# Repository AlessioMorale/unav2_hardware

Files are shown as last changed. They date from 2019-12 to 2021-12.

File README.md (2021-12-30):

View this project on [CADLAB.io](https://cadlab.io/project/25058). 

# unav2_hardware
Initial test hardware for the future STM32F4 based uNav motor controller

## baseboard
An initial, unfinished and untested attempt to design a modular design.

## integrated_board
This is the first iteration of the testing hardware. It is being built but is not tested yet.
[more information](integrated_board/README.md)

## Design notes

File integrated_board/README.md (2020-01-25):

# Integrated Board
This is the first iteration of test hardware for unav2. The board includes a STM32F405 and two DRV8871 drivers.
It supports motor current feedback using two INA186 and global battery current/voltage monitor using an INA219.
Additionally there is an LM75 temperature monitor ic and a fan output.

Link to [Interactive BOM](https://htmlpreview.github.io/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) (built with the awesome [InteractiveHtmlBom plugin](https://github.com/openscopeproject/InteractiveHtmlBom) )

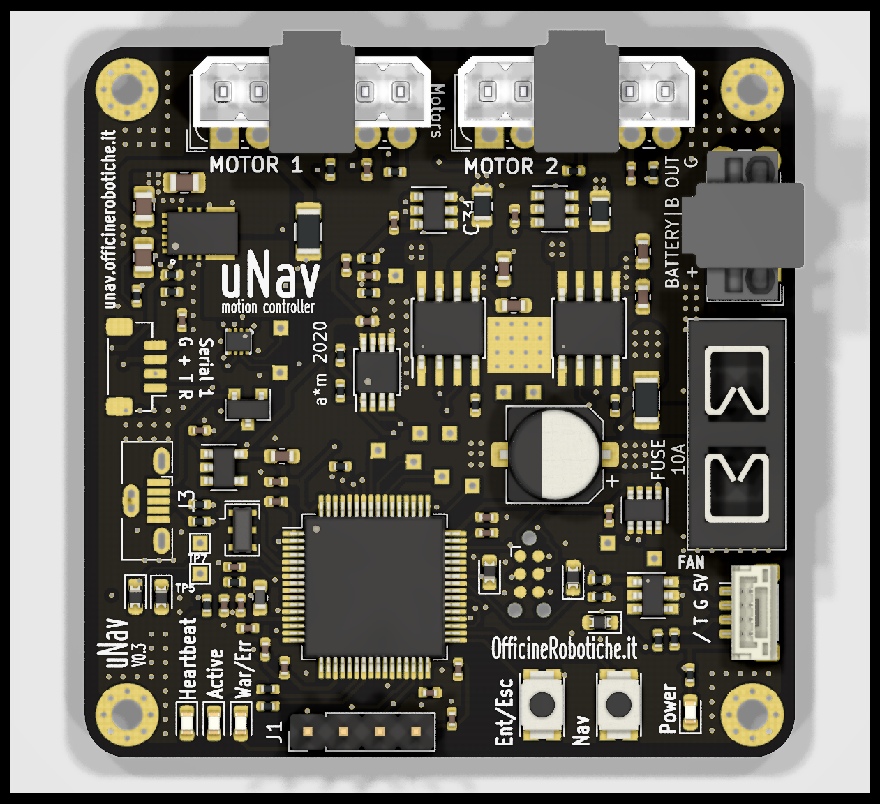
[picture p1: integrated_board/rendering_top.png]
Board top

Note: Encoder, serial and fan connectors are actually JST SH series, not exactly the type shown.

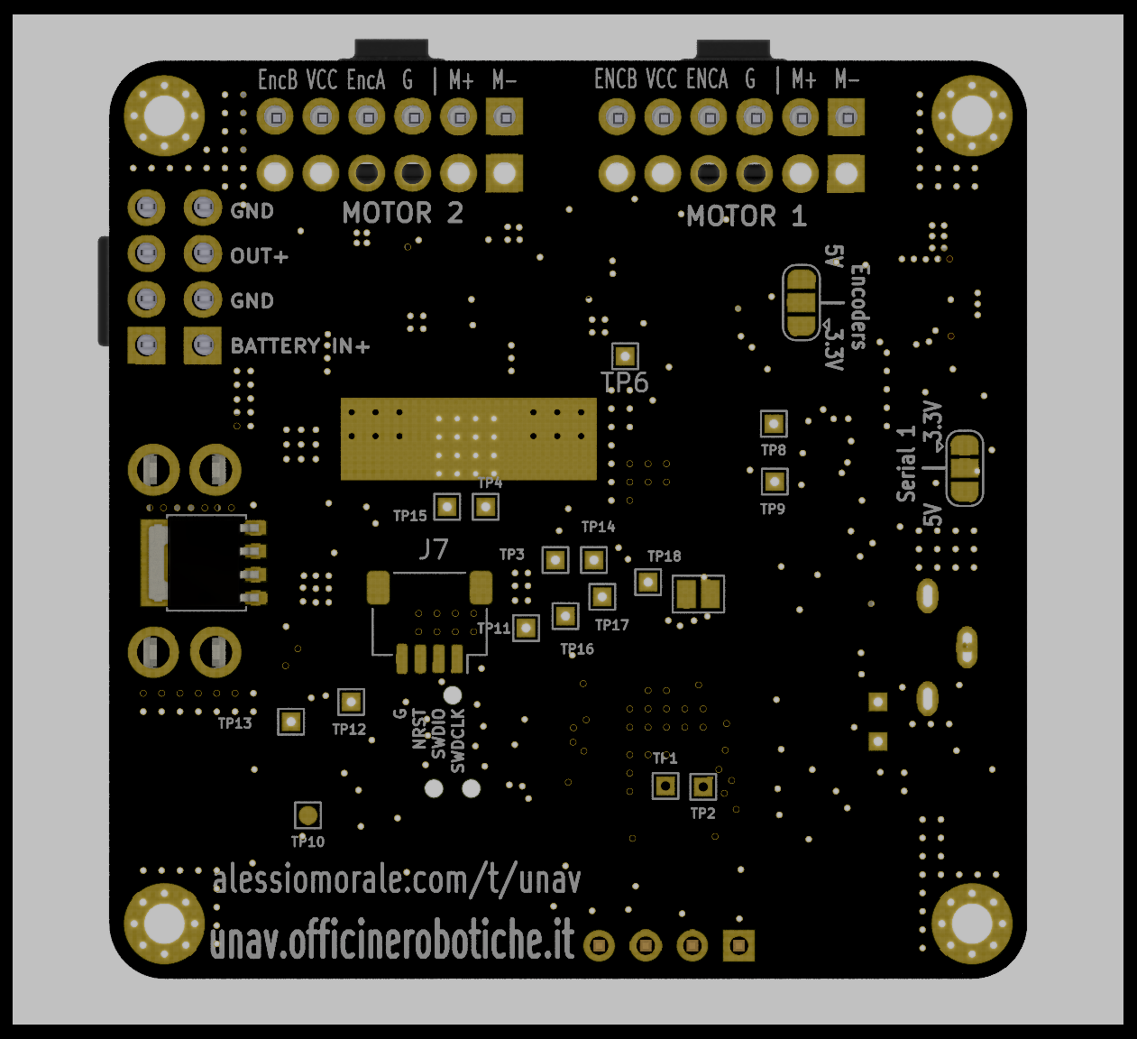
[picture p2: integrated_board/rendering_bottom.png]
Board bottom


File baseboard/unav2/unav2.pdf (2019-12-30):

## unav2 Project Configuration Report

# 1. Description

## 1.1. Project

Project Name | unav2
Board Name | custom
Generated with: | STM32CubeMX 5.2.0
Date | 08/10/2019

## 1.2. MCU

MCU Series | STM32F4
MCU Line | STM32F407/417
MCU name | STM32F407VETx
MCU Package | LQFP100
MCU Pin number | 100

# 2. Pinout Configuration

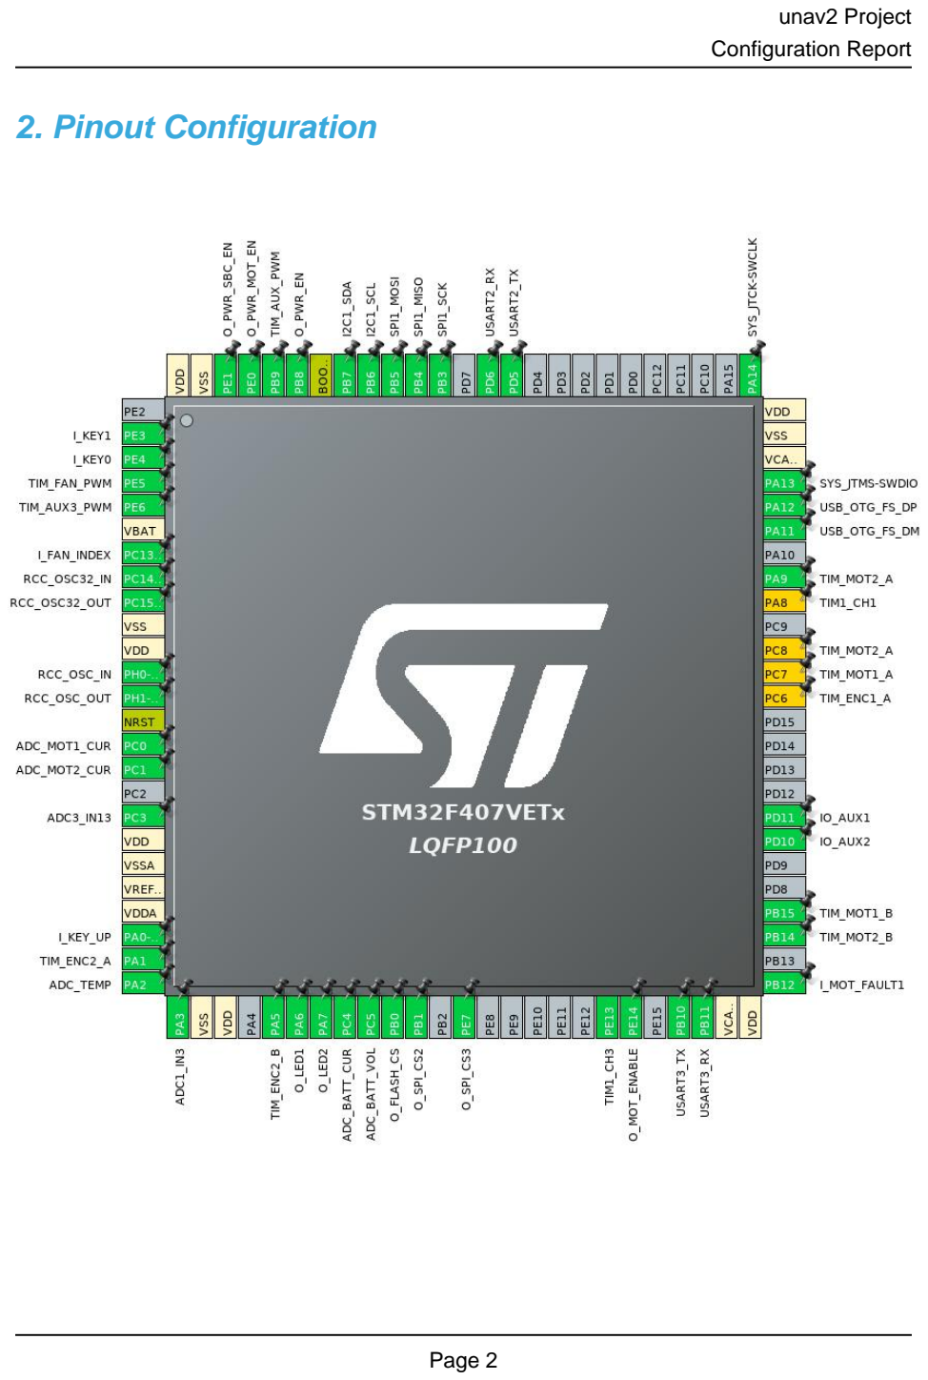
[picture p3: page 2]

# 3. Pins Configuration

Pin Number LQFP100 | Pin Name (function after reset) | Pin Type | Alternate Function(s) | Label
2 | PE3 * | I/O | GPIO_Input | I_KEY1
3 | PE4 * | I/O | GPIO_Input | I_KEY0
4 | PE5 | I/O | TIM9_CH1 | TIM_FAN_PWM
5 | PE6 | I/O | TIM9_CH2 | TIM_AUX3_PWM
6 | VBAT | Power
7 | PC13-ANTI_TAMP * | I/O | GPIO_Input | I_FAN_INDEX
8 | PC14-OSC32_IN | I/O | RCC_OSC32_IN
9 | PC15-OSC32_OUT | I/O | RCC_OSC32_OUT
10 | VSS | Power
11 | VDD | Power
12 | PH0-OSC_IN | I/O | RCC_OSC_IN
13 | PH1-OSC_OUT | I/O | RCC_OSC_OUT
14 | NRST | Reset
15 | PC0 | I/O | ADC2_IN10 | ADC_MOT1_CUR
16 | PC1 | I/O | ADC2_IN11 | ADC_MOT2_CUR
18 | PC3 | I/O | ADC3_IN13
19 | VDD | Power
20 | VSSA | Power
21 | VREF+ | Power
22 | VDDA | Power
23 | PA0-WKUP | I/O | GPIO_EXTI0 | I_KEY_UP
24 | PA1 | I/O | TIM2_CH2 | TIM_ENC2_A
25 | PA2 | I/O | ADC1_IN2 | ADC_TEMP
26 | PA3 | I/O | ADC1_IN3
27 | VSS | Power
28 | VDD | Power
30 | PA5 | I/O | TIM2_CH1 | TIM_ENC2_B
31 | PA6 | I/O | TIM13_CH1 | O_LED1
32 | PA7 | I/O | TIM14_CH1 | O_LED2
33 | PC4 | I/O | ADC1_IN14 | ADC_BATT_CUR
34 | PC5 | I/O | ADC1_IN15 | ADC_BATT_VOL
35 | PB0 * | I/O | GPIO_Output | O_FLASH_CS
36 | PB1 * | I/O | GPIO_Output | O_SPI_CS2
38 | PE7 * | I/O | GPIO_Output | O_SPI_CS3
44 | PE13 | I/O | TIM1_CH3
45 | PE14 * | I/O | GPIO_Output | O_MOT_ENABLE

Pin Number LQFP100 | Pin Name (function after reset) | Pin Type | Alternate Function(s) | Label
47 | PB10 | I/O | USART3_TX
48 | PB11 | I/O | USART3_RX
49 | VCAP_1 | Power
50 | VDD | Power
51 | PB12 | I/O | GPIO_EXTI12 | I_MOT_FAULT1
53 | PB14 | I/O | TIM1_CH2N | TIM_MOT2_B
54 | PB15 | I/O | TIM1_CH3N | TIM_MOT1_B
57 | PD10 * | I/O | GPIO_Input | IO_AUX2
58 | PD11 * | I/O | GPIO_Output | IO_AUX1
63 | PC6 ** | I/O | TIM3_CH1 | TIM_ENC1_A
64 | PC7 ** | I/O | TIM8_CH2 | TIM_MOT1_A
65 | PC8 ** | I/O | TIM8_CH3 | TIM_MOT2_A
67 | PA8 ** | I/O | TIM1_CH1
68 | PA9 | I/O | TIM1_CH2 | TIM_MOT2_A
70 | PA11 | I/O | USB_OTG_FS_DM
71 | PA12 | I/O | USB_OTG_FS_DP
72 | PA13 | I/O | SYS_JTMS-SWDIO
73 | VCAP_2 | Power
74 | VSS | Power
75 | VDD | Power
76 | PA14 | I/O | SYS_JTCK-SWCLK
86 | PD5 | I/O | USART2_TX
87 | PD6 | I/O | USART2_RX
89 | PB3 | I/O | SPI1_SCK
90 | PB4 | I/O | SPI1_MISO
91 | PB5 | I/O | SPI1_MOSI
92 | PB6 | I/O | I2C1_SCL
93 | PB7 | I/O | I2C1_SDA
94 | BOOT0 | Boot
95 | PB8 * | I/O | GPIO_Output | O_PWR_EN
96 | PB9 | I/O | TIM11_CH1 | TIM_AUX_PWM
97 | PE0 * | I/O | GPIO_Output | O_PWR_MOT_EN
98 | PE1 * | I/O | GPIO_Output | O_PWR_SBC_EN
99 | VSS | Power
100 | VDD | Power

## * The pin is affected with an I/O function ** The pin is affected with a peripheral function but no peripheral mode is activated

# 4. Clock Tree Configuration

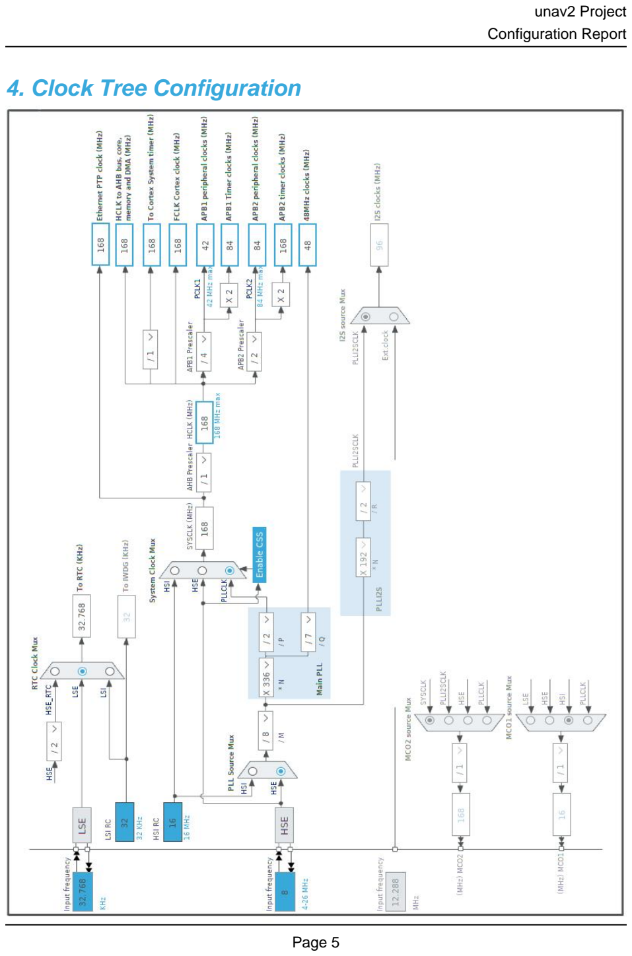
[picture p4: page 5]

# 5. Software Project

## 5.1. Project Settings

Name | Value
Project Name | unav2
Project Folder | /home/alessio/code/hardware/unav2/baseboard/unav2
Toolchain / IDE | Makefile
Firmware Package Name and Version | STM32Cube FW_F4 V1.24.1

## 5.2. Code Generation Settings

Name | Value
STM32Cube Firmware Library Package | Copy all used libraries into the project folder
Generate peripheral initialization as a pair of '.c/.h' files | Yes
Backup previously generated files when re-generating | No
Delete previously generated files when not re-generated | No
Set all free pins as analog (to optimize the power consumption) | No

# 6. Power Consumption Calculator report

### 6.1. Microcontroller Selection

Series | STM32F4
Line | STM32F407/417
MCU | STM32F407VETx
Datasheet | 022152_Rev8

### 6.2. Parameter Selection

Temperature | 25
Vdd | 3.3

# 7. IPs and Middleware Configuration

# 7.1. ADC1

## mode: IN2 mode: IN3 mode: IN14 mode: IN15 mode: Temperature Sensor Channel mode: Vrefint Channel mode: Vbat Channel 7.1.1. Parameter Settings:

### ADCs_Common_Settings:

Mode | Independent mode

### ADC_Settings:

Clock Prescaler | PCLK2 divided by 6 *
Resolution | 12 bits (15 ADC Clock cycles)
Data Alignment | Right alignment
Scan Conversion Mode | Disabled
Continuous Conversion Mode | Disabled
Discontinuous Conversion Mode | Disabled
DMA Continuous Requests | Disabled
End Of Conversion Selection | EOC flag at the end of single channel conversion

### ADC_Regular_ConversionMode:

Number Of Conversion | 1
External Trigger Conversion Source | Regular Conversion launched by software
External Trigger Conversion Edge | None
Rank | 1
Channel | Channel Vbat *
Sampling Time | 3 Cycles

### ADC_Injected_ConversionMode:

Number Of Conversions | 0

### WatchDog:

Enable Analog WatchDog Mode | false

# 7.2. ADC2

## mode: IN10 mode: IN11 7.2.1. Parameter Settings:

### ADCs_Common_Settings:

Mode | Independent mode

### ADC_Settings:

Clock Prescaler | PCLK2 divided by 6 *
Resolution | 12 bits (15 ADC Clock cycles)
Data Alignment | Right alignment
Scan Conversion Mode | Enabled
Continuous Conversion Mode | Disabled
Discontinuous Conversion Mode | Enabled *
Number Of Discontinuous Conversions | 1
DMA Continuous Requests | Enabled *
End Of Conversion Selection | EOC flag at the end of all conversions *

### ADC_Regular_ConversionMode:

Number Of Conversion | 4 *
External Trigger Conversion Source | Timer 8 Trigger Out event *
External Trigger Conversion Edge | Trigger detection on the rising edge
Rank | 1
Channel | Channel 10
Sampling Time | 28 Cycles *
Rank | 2 *
Channel | Channel 11 *
Sampling Time | 28 Cycles *
Rank | 3 *
Channel | Channel 10
Sampling Time | 28 Cycles *
Rank | 4 *
Channel | Channel 11 *
Sampling Time | 28 Cycles *

### ADC_Injected_ConversionMode:

Number Of Conversions | 0

### WatchDog:

Enable Analog WatchDog Mode | false

# 7.3. ADC3

## mode: IN13 7.3.1. Parameter Settings:

### ADCs_Common_Settings:

Mode | Independent mode

### ADC_Settings:

Clock Prescaler | PCLK2 divided by 6 *
Resolution | 12 bits (15 ADC Clock cycles)
Data Alignment | Right alignment
Scan Conversion Mode | Disabled
Continuous Conversion Mode | Disabled
Discontinuous Conversion Mode | Disabled
DMA Continuous Requests | Disabled
End Of Conversion Selection | EOC flag at the end of single channel conversion

### ADC_Regular_ConversionMode:

Number Of Conversion | 1
External Trigger Conversion Source | Regular Conversion launched by software
External Trigger Conversion Edge | None
Rank | 1
Channel | Channel 13
Sampling Time | 3 Cycles

### ADC_Injected_ConversionMode:

Number Of Conversions | 0

### WatchDog:

Enable Analog WatchDog Mode | false

# 7.4. I2C1

## I2C: I2C 7.4.1. Parameter Settings:

### Master Features:

I2C Speed Mode | Standard Mode
I2C Clock Speed (Hz) | 100000

### Slave Features:

Clock No Stretch Mode | Disabled
Primary Address Length selection | 7-bit

Dual Address Acknowledged | Disabled
Primary slave address | 0
General Call address detection | Disabled

# 7.5. RCC

## High Speed Clock (HSE): Crystal/Ceramic Resonator Low Speed Clock (LSE) : Crystal/Ceramic Resonator 7.5.1. Parameter Settings:

### System Parameters:

VDD voltage (V) | 3.3
Instruction Cache | Enabled
Prefetch Buffer | Enabled
Data Cache | Enabled
Flash Latency(WS) | 5 WS (6 CPU cycle)

### RCC Parameters:

HSI Calibration Value | 16
HSE Startup Timout Value (ms) | 100
LSE Startup Timout Value (ms) | 5000

### Power Parameters:

Power Regulatror Voltage Scale | Power Regulator Voltage Scale 1

# 7.6. RTC

## mode: Activate Clock Source mode: Activate Calendar 7.6.1. Parameter Settings:

### General:

Hour Format | Hourformat 24
Asynchronous Predivider value | 127
Synchronous Predivider value | 255

### Calendar Time:

Data Format | BCD data format
Hours | 0
Minutes | 0
Seconds | 0
Day Light Saving: value of hour adjustment | Daylightsaving None

Store Operation | Storeoperation Reset

### Calendar Date:

Week Day | Thursday *
Month | July *
Date | 7 *
Year | 18 *

# 7.7. SPI1

## Mode: Full-Duplex Master 7.7.1. Parameter Settings:

### Basic Parameters:

Frame Format | Motorola
Data Size | 8 Bits
First Bit | MSB First

### Clock Parameters:

Prescaler (for Baud Rate) | 2
Baud Rate | 42.0 MBits/s *
Clock Polarity (CPOL) | Low
Clock Phase (CPHA) | 1 Edge

### Advanced Parameters:

CRC Calculation | Disabled
NSS Signal Type | Software

# 7.8. SYS

## Debug: Serial Wire Timebase Source: TIM10

# 7.9. TIM1

## Clock Source : Internal Clock Channel2: PWM Generation CH2 CH2N Channel3: Output Compare CH3 CH3N 7.9.1. Parameter Settings:

### Counter Settings:

Prescaler (PSC - 16 bits value) | 7 *
Counter Mode | Up
Counter Period (AutoReload Register - 16 bits value ) | 1024 *
Internal Clock Division (CKD) | No Division
Repetition Counter (RCR - 8 bits value) | 0
auto-reload preload | Enable *

### Trigger Output (TRGO) Parameters:

Master/Slave Mode (MSM bit) | Disable (Trigger input effect not delayed)
Trigger Event Selection | Reset (UG bit from TIMx_EGR)

### Break And Dead Time management - BRK Configuration:

BRK State | Disable
BRK Polarity | High

### Break And Dead Time management - Output Configuration:

Automatic Output State | Disable
Off State Selection for Run Mode (OSSR) | Disable
Off State Selection for Idle Mode (OSSI) | Disable
Lock Configuration | Off
Dead Time | 2 *

### PWM Generation Channel 2 and 2N:

Mode | PWM mode 1
Pulse (16 bits value) | 512 *
Fast Mode | Disable
CH Polarity | High
CHN Polarity | High
CH Idle State | Reset
CHN Idle State | Reset

### Output Compare Channel 3 and 3N:

Mode | Frozen (used for Timing base)
Pulse (16 bits value) | 0
CH Polarity | High
CHN Polarity | High
CH Idle State | Reset
CHN Idle State | Reset

# 7.10. TIM2

## Combined Channels: Encoder Mode 7.10.1. Parameter Settings:

### Counter Settings:

Prescaler (PSC - 16 bits value) | 0
Counter Mode | Up
Counter Period (AutoReload Register - 32 bits value ) | 65535 *
Internal Clock Division (CKD) | No Division
auto-reload preload | Disable

### Trigger Output (TRGO) Parameters:

Master/Slave Mode (MSM bit) | Disable (Trigger input effect not delayed)
Trigger Event Selection | Reset (UG bit from TIMx_EGR)

### Encoder:

Encoder Mode | Encoder Mode TI1 and TI2 *

____ Parameters for Channel 1 ____
Polarity | Rising Edge
IC Selection | Direct
Prescaler Division Ratio | No division
Input Filter | 0
____ Parameters for Channel 2 ____
Polarity | Rising Edge
IC Selection | Direct
Prescaler Division Ratio | No division
Input Filter | 0

# 7.11. TIM8

## Clock Source : Internal Clock Channel1: Output Compare No Output 7.11.1. Parameter Settings:

### Counter Settings:

Prescaler (PSC - 16 bits value) | 168 *
Counter Mode | Up
Counter Period (AutoReload Register - 16 bits value ) | 1000 *
Internal Clock Division (CKD) | No Division
Repetition Counter (RCR - 8 bits value) | 0
auto-reload preload | Enable *

### Trigger Output (TRGO) Parameters:

Master/Slave Mode (MSM bit) | Disable (Trigger input effect not delayed)
Trigger Event Selection | Update Event *

### Break And Dead Time management - BRK Configuration:

BRK State | Disable
BRK Polarity | High

### Break And Dead Time management - Output Configuration:

Automatic Output State | Disable
Off State Selection for Run Mode (OSSR) | Disable
Off State Selection for Idle Mode (OSSI) | Disable
Lock Configuration | Off

### Output Compare No Output Channel 1:

Mode | Active Level on match *
Pulse (16 bits value) | 0
CH Polarity | High
CH Idle State | Reset

# 7.12. TIM9

## mode: Clock Source Channel1: PWM Generation CH1 Channel2: PWM Generation CH2 7.12.1. Parameter Settings:

### Counter Settings:

Prescaler (PSC - 16 bits value) | 15 *
Counter Mode | Up
Counter Period (AutoReload Register - 16 bits value ) | 4096 *
Internal Clock Division (CKD) | No Division
auto-reload preload | Enable *

### PWM Generation Channel 1:

Mode | PWM mode 1
Pulse (16 bits value) | 0
Fast Mode | Disable
CH Polarity | High

### PWM Generation Channel 2:

Mode | PWM mode 1
Pulse (16 bits value) | 0
Fast Mode | Disable
CH Polarity | High

# 7.13. TIM11

## mode: Activated Channel1: PWM Generation CH1 7.13.1. Parameter Settings:

### Counter Settings:

Prescaler (PSC - 16 bits value) | 0
Counter Mode | Up
Counter Period (AutoReload Register - 16 bits value ) | 0
Internal Clock Division (CKD) | No Division
auto-reload preload | Disable

### PWM Generation Channel 1:

Mode | PWM mode 1
Pulse (16 bits value) | 0
Fast Mode | Disable
CH Polarity | High

# 7.14. TIM13

## mode: Activated Channel1: PWM Generation CH1 7.14.1. Parameter Settings:

### Counter Settings:

Prescaler (PSC - 16 bits value) | 15 *
Counter Mode | Up
Counter Period (AutoReload Register - 16 bits value ) | 1024 *
Internal Clock Division (CKD) | No Division
auto-reload preload | Enable *

### PWM Generation Channel 1:

Mode | PWM mode 1
Pulse (16 bits value) | 0
Fast Mode | Disable
CH Polarity | High

# 7.15. TIM14

## mode: Activated Channel1: PWM Generation CH1 7.15.1. Parameter Settings:

### Counter Settings:

Prescaler (PSC - 16 bits value) | 15 *
Counter Mode | Up
Counter Period (AutoReload Register - 16 bits value ) | 1024 *
Internal Clock Division (CKD) | No Division
auto-reload preload | Enable *

### PWM Generation Channel 1:

Mode | PWM mode 1
Pulse (16 bits value) | 0
Fast Mode | Disable
CH Polarity | High

# 7.16. USART2

## Mode: Asynchronous 7.16.1. Parameter Settings:

### Basic Parameters:

Baud Rate | 115200
Word Length | 8 Bits (including Parity)
Parity | None
Stop Bits | 1

### Advanced Parameters:

Data Direction | Receive and Transmit
Over Sampling | 16 Samples

# 7.17. USART3

## Mode: Asynchronous 7.17.1. Parameter Settings:

### Basic Parameters:

Baud Rate | 115200
Word Length | 8 Bits (including Parity)
Parity | None
Stop Bits | 1

### Advanced Parameters:

Data Direction | Receive and Transmit
Over Sampling | 16 Samples

# 7.18. USB_OTG_FS

## Mode: Device_Only 7.18.1. Parameter Settings:

Speed | Device Full Speed 12MBit/s
Low power | Disabled
Link Power Management | Disabled
VBUS sensing | Disabled
Signal start of frame | Disabled

# 7.19. FREERTOS

## Interface: CMSIS_V1 7.19.1. Config parameters:

### API:

FreeRTOS API | CMSIS v1

### Versions:

FreeRTOS version | 10.0.1
CMSIS-RTOS version | 1.02

### Kernel settings:

USE_PREEMPTION | Enabled
CPU_CLOCK_HZ | SystemCoreClock
TICK_RATE_HZ | 1000
MAX_PRIORITIES | 7
MINIMAL_STACK_SIZE | 128
MAX_TASK_NAME_LEN | 16
USE_16_BIT_TICKS | Disabled
IDLE_SHOULD_YIELD | Enabled
USE_MUTEXES | Enabled

USE_RECURSIVE_MUTEXES | Enabled *
USE_COUNTING_SEMAPHORES | Disabled
QUEUE_REGISTRY_SIZE | 8
USE_APPLICATION_TASK_TAG | Disabled
ENABLE_BACKWARD_COMPATIBILITY | Enabled
USE_PORT_OPTIMISED_TASK_SELECTION | Enabled
USE_TICKLESS_IDLE | Disabled
USE_TASK_NOTIFICATIONS | Enabled
RECORD_STACK_HIGH_ADDRESS | Disabled

### Memory management settings:

Memory Allocation | Dynamic / Static
TOTAL_HEAP_SIZE | 65535 *
Memory Management scheme | heap_4

### Hook function related definitions:

USE_IDLE_HOOK | Disabled
USE_TICK_HOOK | Disabled
USE_MALLOC_FAILED_HOOK | Disabled
USE_DAEMON_TASK_STARTUP_HOOK | Disabled
CHECK_FOR_STACK_OVERFLOW | Disabled

### Run time and task stats gathering related definitions:

GENERATE_RUN_TIME_STATS | Enabled *
USE_TRACE_FACILITY | Disabled
USE_STATS_FORMATTING_FUNCTIONS | Disabled

### Co-routine related definitions:

USE_CO_ROUTINES | Disabled
MAX_CO_ROUTINE_PRIORITIES | 2

### Software timer definitions:

USE_TIMERS | Disabled

### Interrupt nesting behaviour configuration:

LIBRARY_LOWEST_INTERRUPT_PRIORITY | 15
LIBRARY_MAX_SYSCALL_INTERRUPT_PRIORITY | 5

## 7.19.2. Include parameters:

### Include definitions:

vTaskPrioritySet | Enabled
uxTaskPriorityGet | Enabled
vTaskDelete | Enabled
vTaskCleanUpResources | Disabled
vTaskSuspend | Enabled

vTaskDelayUntil | Enabled *
vTaskDelay | Enabled
xTaskGetSchedulerState | Enabled
xTaskResumeFromISR | Enabled
xQueueGetMutexHolder | Disabled
xSemaphoreGetMutexHolder | Disabled
pcTaskGetTaskName | Disabled
uxTaskGetStackHighWaterMark | Enabled *
xTaskGetCurrentTaskHandle | Disabled
eTaskGetState | Disabled
xEventGroupSetBitFromISR | Disabled
xTimerPendFunctionCall | Disabled
xTaskAbortDelay | Disabled
xTaskGetHandle | Disabled

# 7.20. USB_DEVICE

## Class For FS IP: Communication Device Class (Virtual Port Com) 7.20.1. Parameter Settings:

### Basic Parameters:

USBD_MAX_NUM_INTERFACES (Maximum number of supported interfaces) | 8 *
USBD_MAX_NUM_CONFIGURATION (Maximum number of supported configuration) | 1
USBD_MAX_STR_DESC_SIZ (Maximum size for the string descriptors) | 0x200
USBD_SUPPORT_USER_STRING (Enable user string descriptor) | Disabled
USBD_SELF_POWERED (Enabled self power) | Enabled
USBD_DEBUG_LEVEL (USBD Debug Level) | 0: No debug message

### Class Parameters:

USB CDC Rx Buffer Size | 2048
USB CDC Tx Buffer Size | 2048

## 7.20.2. Device Descriptor:

### Device Descriptor:

VID (Vendor IDentifier) | 1155
LANGID_STRING (Language Identifier) | English(United States)
MANUFACTURER_STRING (Manufacturer Identifier) | STMicroelectronics

### Device Descriptor FS:

PID (Product IDentifier) | 22336
PRODUCT_STRING (Product Identifier)

| UNAVng *
CONFIGURATION_STRING (Configuration Identifier) | CDC Config
INTERFACE_STRING (Interface Identifier) | CDC Interface

### * User modified value

# 8. System Configuration

# 8.1. GPIO configuration

IP | Pin | Signal | GPIO mode | GPIO pull/up pull down

## Max Speed

## User Label

ADC1 | PA2 | ADC1_IN2 | Analog mode | No pull-up and no pull-down | n/a | ADC_TEMP
| PA3 | ADC1_IN3 | Analog mode | No pull-up and no pull-down | n/a
| PC4 | ADC1_IN14 | Analog mode | No pull-up and no pull-down | n/a | ADC_BATT_CUR
| PC5 | ADC1_IN15 | Analog mode | No pull-up and no pull-down | n/a | ADC_BATT_VOL
ADC2 | PC0 | ADC2_IN10 | Analog mode | No pull-up and no pull-down | n/a | ADC_MOT1_CUR
| PC1 | ADC2_IN11 | Analog mode | No pull-up and no pull-down | n/a | ADC_MOT2_CUR
ADC3 | PC3 | ADC3_IN13 | Analog mode | No pull-up and no pull-down | n/a
I2C1 | PB6 | I2C1_SCL | Alternate Function Open Drain | Pull-up | Very High
*
| PB7 | I2C1_SDA | Alternate Function Open Drain | Pull-up | Very High
*
RCC | PC14- OSC32_IN | RCC_OSC32_IN | n/a | n/a | n/a
| PC15- OSC32_OU T | RCC_OSC32_O UT | n/a | n/a | n/a

PH0-
OSC_IN
| | RCC_OSC_IN | n/a | n/a | n/a
| PH1- OSC_OUT | RCC_OSC_OUT | n/a | n/a | n/a
SPI1 | PB3 | SPI1_SCK | Alternate Function Push Pull | No pull-up and no pull-down | Very High
*
| PB4 | SPI1_MISO | Alternate Function Push Pull | No pull-up and no pull-down | Very High
*
| PB5 | SPI1_MOSI | Alternate Function Push Pull | No pull-up and no pull-down | Very High
*
SYS | PA13 | SYS_JTMS- SWDIO | n/a | n/a | n/a
| PA14 | SYS_JTCK- SWCLK | n/a | n/a | n/a
TIM1 | PE13 | TIM1_CH3 | Alternate Function Push Pull | No pull-up and no pull-down | Low
| PB14 | TIM1_CH2N | Alternate Function Push Pull | No pull-up and no pull-down | Low | TIM_MOT2_B
| PB15 | TIM1_CH3N | Alternate Function Push Pull | No pull-up and no pull-down | Low | TIM_MOT1_B
| PA9 | TIM1_CH2 | Alternate Function Push Pull | No pull-up and no pull-down | Low | TIM_MOT2_A
TIM2 | PA1 | TIM2_CH2 | Alternate Function Push Pull | No pull-up and no pull-down | Low | TIM_ENC2_A
| PA5 | TIM2_CH1 | Alternate Function Push Pull | No pull-up and no pull-down | Low | TIM_ENC2_B

IP | Pin | Signal | GPIO mode | GPIO pull/up pull down | Max Speed | User Label
TIM9 | PE5 | TIM9_CH1 | Alternate Function Push Pull | No pull-up and no pull-down | Low | TIM_FAN_PWM
| PE6 | TIM9_CH2 | Alternate Function Push Pull | No pull-up and no pull-down | Low | TIM_AUX3_PWM
TIM11 | PB9 | TIM11_CH1 | Alternate Function Push Pull | No pull-up and no pull-down | Low | TIM_AUX_PWM
TIM13 | PA6 | TIM13_CH1 | Alternate Function Push Pull | No pull-up and no pull-down | Low | O_LED1
TIM14 | PA7 | TIM14_CH1 | Alternate Function Push Pull | No pull-up and no pull-down | Low | O_LED2
USART2 | PD5 | USART2_TX | Alternate Function Push Pull | Pull-up | Very High *
| PD6 | USART2_RX | Alternate Function Push Pull | Pull-up | Very High *
USART3 | PB10 | USART3_TX | Alternate Function Push Pull | Pull-up | Very High *
| PB11 | USART3_RX | Alternate Function Push Pull | Pull-up | Very High *
USB_OTG_ FS | PA11 | USB_OTG_FS_ DM | Alternate Function Push Pull | No pull-up and no pull-down | Very High *
| PA12 | USB_OTG_FS_ DP | Alternate Function Push Pull | No pull-up and no pull-down | Very High *
Single Mapped Signals | PC6 | TIM3_CH1 | Alternate Function Push Pull | No pull-up and no pull-down | Low | TIM_ENC1_A
| PC7 | TIM8_CH2 | Alternate Function Push Pull | No pull-up and no pull-down | Low | TIM_MOT1_A
| PC8 | TIM8_CH3 | Alternate Function Push Pull | No pull-up and no pull-down | Low | TIM_MOT2_A
| PA8 | TIM1_CH1 | Alternate Function Push Pull | No pull-up and no pull-down | Low
GPIO | PE3 | GPIO_Input | Input mode | No pull-up and no pull-down | n/a | I_KEY1
| PE4 | GPIO_Input | Input mode | No pull-up and no pull-down | n/a | I_KEY0
| PC13-ANTI_TAMP | GPIO_Input | Input mode | No pull-up and no pull-down | n/a | I_FAN_INDEX
| PA0-WKUP | GPIO_EXTI0 | External Interrupt Mode with Rising edge trigger detection | No pull-up and no pull-down | n/a | I_KEY_UP
| PB0 | GPIO_Output | Output Push Pull | No pull-up and no pull-down | Low | O_FLASH_CS
| PB1 | GPIO_Output | Output Push Pull | No pull-up and no pull-down | Low | O_SPI_CS2
| PE7 | GPIO_Output | Output Push Pull | No pull-up and no pull-down | Low | O_SPI_CS3
| PE14 | GPIO_Output | Output Push Pull | No pull-up and no pull-down | Low | O_MOT_ENABLE
| PB12 | GPIO_EXTI12 | External Interrupt Mode with Rising edge trigger detection | No pull-up and no pull-down | n/a | I_MOT_FAULT1
| PD10 | GPIO_Input | Input mode | No pull-up and no pull-down | n/a | IO_AUX2
| PD11 | GPIO_Output | Output Push Pull | No pull-up and no pull-down | Low | IO_AUX1
| PB8 | GPIO_Output | Output Push Pull | No pull-up and no pull-down | Low | O_PWR_EN
| PE0 | GPIO_Output | Output Push Pull | No pull-up and no pull-down | Low | O_PWR_MOT_EN
| PE1 | GPIO_Output | Output Push Pull | No pull-up and no pull-down | Low | O_PWR_SBC_EN

# 8.2. DMA configuration

DMA request | Stream | Direction | Priority
USART2_RX | DMA1_Stream5 | Peripheral To Memory | Medium *
USART2_TX | DMA1_Stream6 | Memory To Peripheral | Medium *
USART3_RX | DMA1_Stream1 | Peripheral To Memory | Medium *
USART3_TX | DMA1_Stream3 | Memory To Peripheral | Medium *
ADC2 | DMA2_Stream2 | Peripheral To Memory | High *

## USART2_RX: DMA1_Stream5 DMA request Settings:

Mode: | Normal
Use fifo: | Disable
Peripheral Increment: | Disable
Memory Increment: | Enable *
Peripheral Data Width: | Byte
Memory Data Width: | Byte

## USART2_TX: DMA1_Stream6 DMA request Settings:

Mode: | Normal
Use fifo: | Disable
Peripheral Increment: | Disable
Memory Increment: | Enable *
Peripheral Data Width: | Byte
Memory Data Width: | Byte

## USART3_RX: DMA1_Stream1 DMA request Settings:

Mode: | Normal
Use fifo: | Disable
Peripheral Increment: | Disable
Memory Increment: | Enable *
Peripheral Data Width: | Byte
Memory Data Width: | Byte

## USART3_TX: DMA1_Stream3 DMA request Settings:

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

## ADC2: DMA2_Stream2 DMA request Settings:

Mode: | Circular *
Use fifo: | Disable
Peripheral Increment: | Disable
Memory Increment: | Enable *
Peripheral Data Width: | Half Word
Memory Data Width: | Half Word

# 8.3. NVIC configuration

Interrupt Table | Enable | Preenmption Priority | SubPriority
Non maskable interrupt | true | 0 | 0
Hard fault interrupt | true | 0 | 0
Memory management fault | true | 0 | 0
Pre-fetch fault, memory access fault | true | 0 | 0
Undefined instruction or illegal state | true | 0 | 0
System service call via SWI instruction | true | 0 | 0
Debug monitor | true | 0 | 0
Pendable request for system service | true | 15 | 0
System tick timer | true | 15 | 0
DMA1 stream1 global interrupt | true | 5 | 0
DMA1 stream3 global interrupt | true | 5 | 0
DMA1 stream5 global interrupt | true | 5 | 0
DMA1 stream6 global interrupt | true | 5 | 0
TIM1 update interrupt and TIM10 global interrupt | true | 0 | 0
DMA2 stream2 global interrupt | true | 5 | 0
USB On The Go FS global interrupt | true | 5 | 0
PVD interrupt through EXTI line 16 | unused
Flash global interrupt | unused
RCC global interrupt | unused
EXTI line0 interrupt | unused
ADC1, ADC2 and ADC3 global interrupts | unused
TIM1 break interrupt and TIM9 global interrupt | unused
TIM1 trigger and commutation interrupts and TIM11 global interrupt | unused
TIM1 capture compare interrupt | unused
TIM2 global interrupt | unused
I2C1 event interrupt | unused
I2C1 error interrupt | unused
SPI1 global interrupt | unused
USART2 global interrupt | unused
USART3 global interrupt | unused
EXTI line[15:10] interrupts | unused
TIM8 break interrupt and TIM12 global interrupt | unused
TIM8 update interrupt and TIM13 global interrupt | unused
TIM8 trigger and commutation interrupts and TIM14 global interrupt | unused
TIM8 capture compare interrupt | unused
FPU global interrupt | unused

### * User modified value

# 9. Software Pack Report

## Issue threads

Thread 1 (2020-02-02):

[INT_BOARD] BOOT0 polarity is inverted

AlessioMorale, 2020-02-02:
There is an issue with boot0 polarity. It needs to be pulled down and the jumper must be connected between boot0 and 3.3v

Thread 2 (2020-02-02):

[INT_BOARD] Ground plane below stm32 and gnd connections are sub-optimal

AlessioMorale, 2020-02-02:
redesign the ground plane below stm32

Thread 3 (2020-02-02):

[INT_BOARD] Commanding enable and standby supply via R13 needs to be removed

AlessioMorale, 2020-02-02:
Unless the regulator is going to power external circuitry the standby circuit and dc/dc enable is pointless and needs to be removed

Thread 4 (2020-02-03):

ICSP port

gbr1, 2020-02-03:
Could be useful to have tag connector on the same side of buttons?
It should allow to mount the board giving access only to upper side.

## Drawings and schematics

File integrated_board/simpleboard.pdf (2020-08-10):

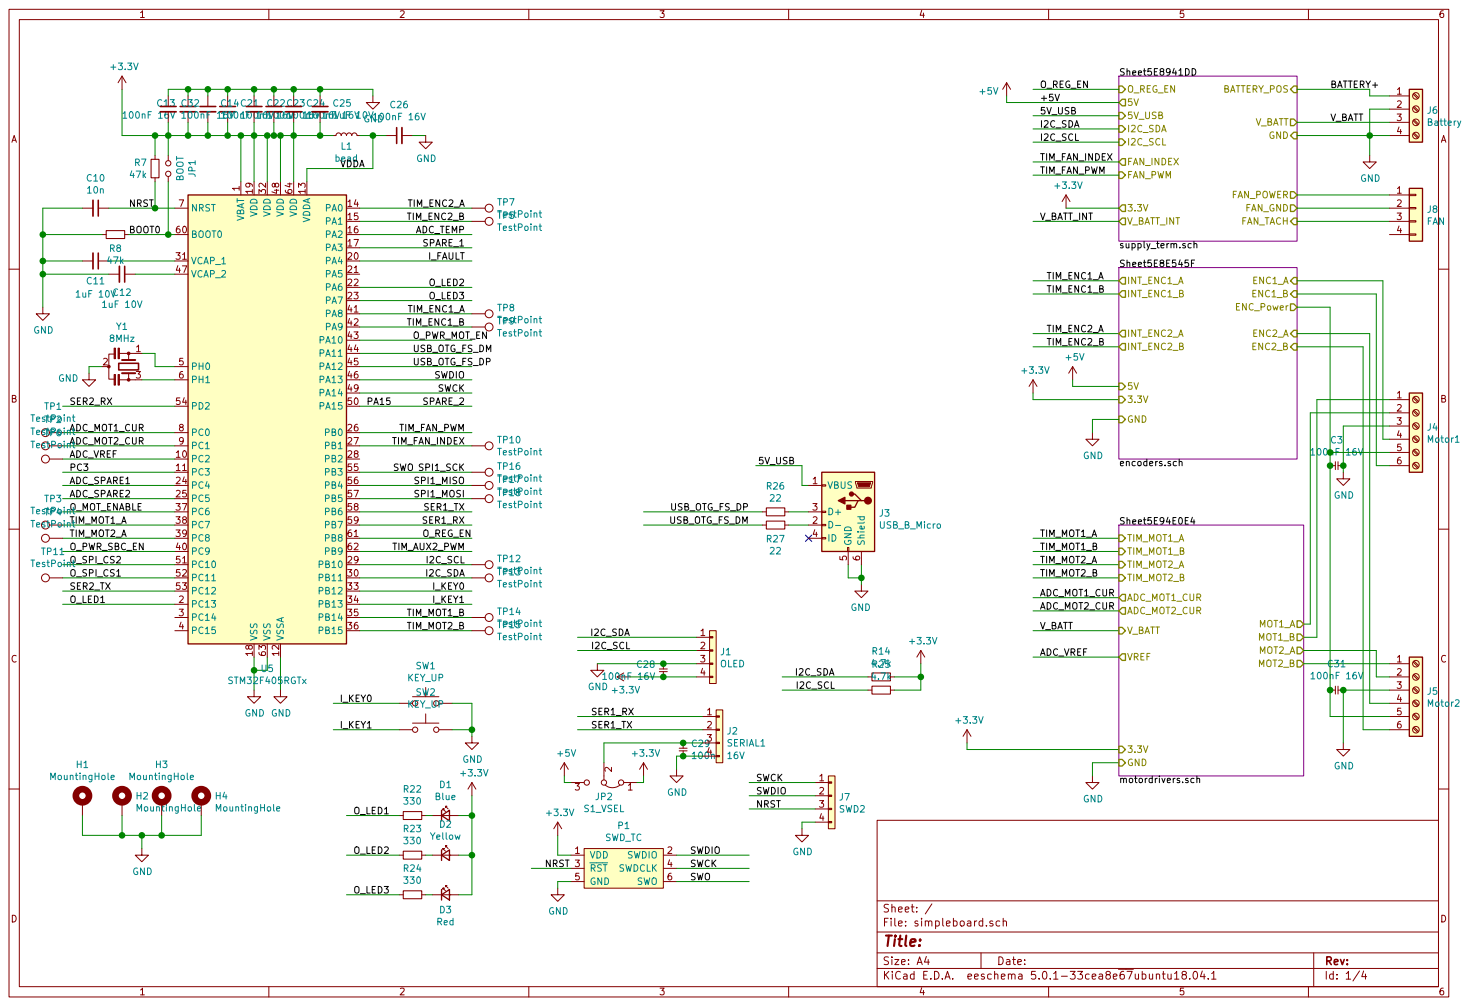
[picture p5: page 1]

1 PC2 10 PC3 11 VSSA 12 VDDA 13 PA0 14 PA1 15 PA2 16 PA3 17 VSS 18 VDD 19 PC13 2 PA4 20 PA5 21 PA6 22 PA7 23 PC4 24 PC5 25 PB0 26 PB1 27 PB2 28 PB10 29 PC14 3 PB11 30 VCAP_1 31 VDD 32 PB12 33 PB13 34 PB14 35 PB15 36 PC6 37 PC7 38 PC8 39 PC15 4 PC9 40 PA8 41 PA9 42 PA10 43 PA11 44 PA12 45 PA13 46 VCAP_2 47 VDD 48 PA14 49 PH0 5 PA15 50 PC10 51 PC11 52 PC12 53 PD2 54 PB3 55 PB4 56 PB5 57 PB6 58 PB7 59 PH1 6 BOOT0 60 PB8 61 PB9 62 VSS 63 VDD 64 NRST 7 PC0 8 PC1 9 U5 STM32F405RGTx

J4Motor1 TP5 TestPoint TP7 TestPoint TP8 TP9 TestPoint TestPoint TP10 TestPoint TP12 TP13 TestPoint TestPoint TP14 TP15 TestPoint TestPoint TP3 TestPoint TP4 TestPoint TP1 TestPoint TP2 TestPoint

File: simpleboard.sch Sheet: /
Id: 1/4 Title:

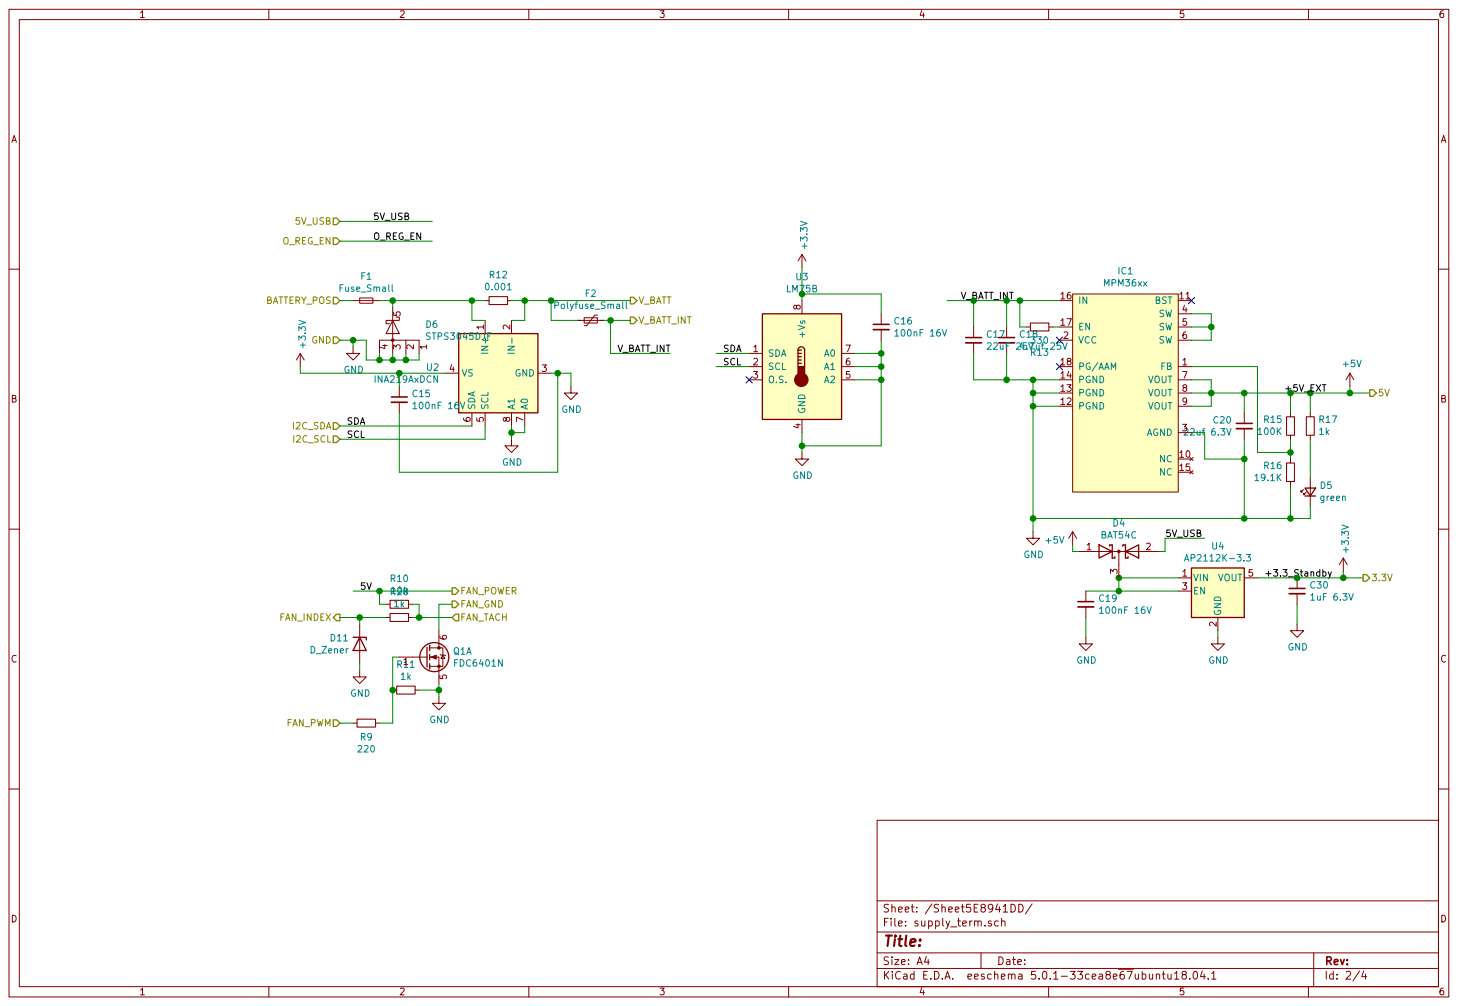
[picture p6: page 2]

1 IN- 2 GND 3 VS 4 SCL
File: supply_term.sch Sheet: /Sheet5E8941DD/ IN+

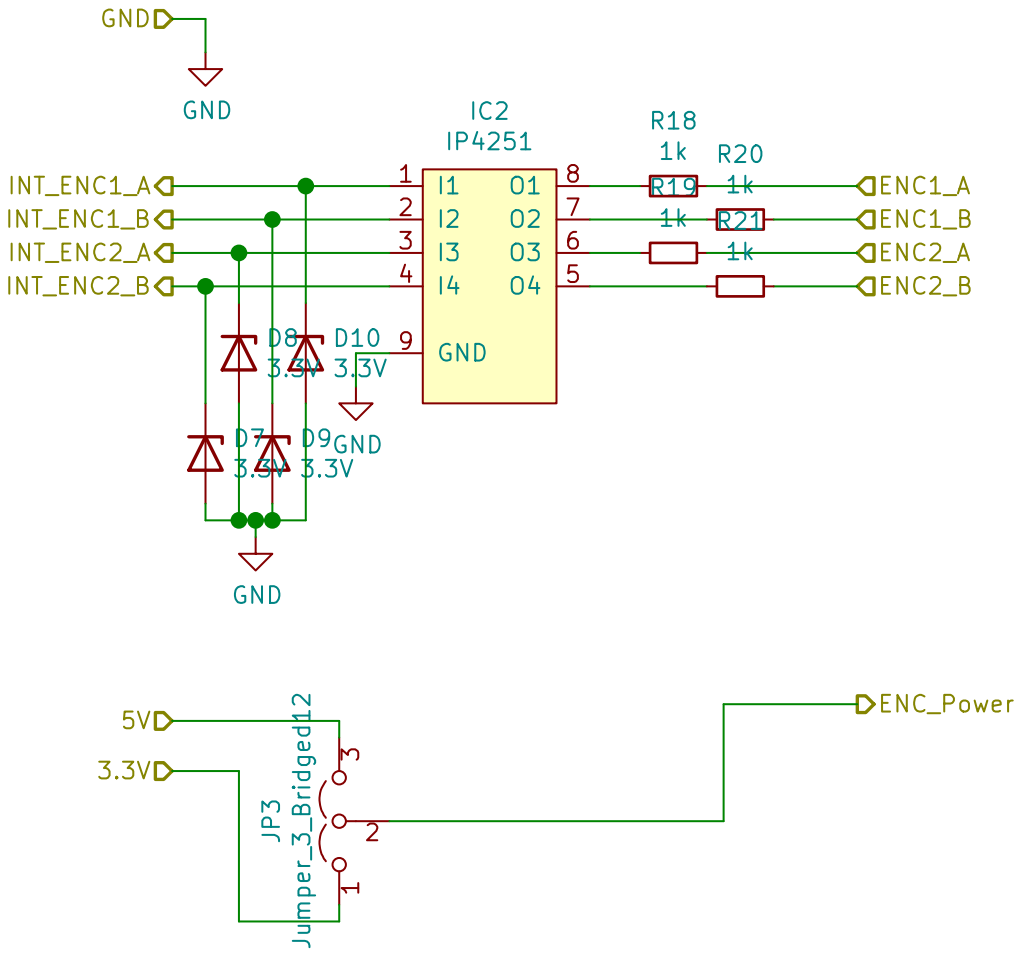
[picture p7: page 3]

Id: 3/4 Title: File: encoders.sch Sheet: /Sheet5E8E545F/

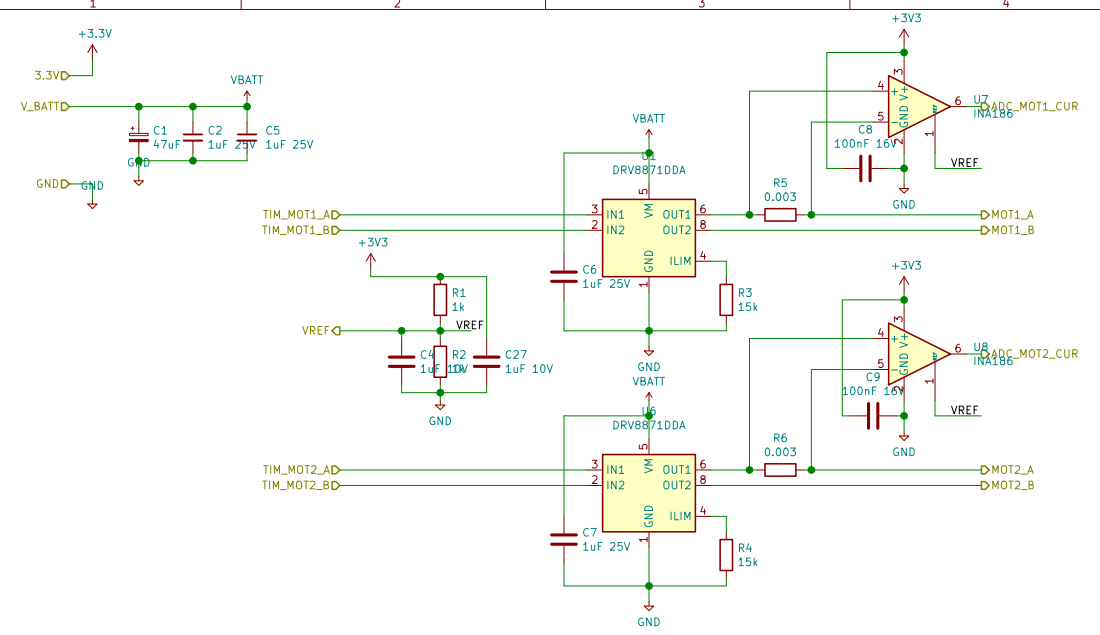
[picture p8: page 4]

Id: 4/4 Title: File: motordrivers.sch Sheet: /Sheet5E94E0E4/

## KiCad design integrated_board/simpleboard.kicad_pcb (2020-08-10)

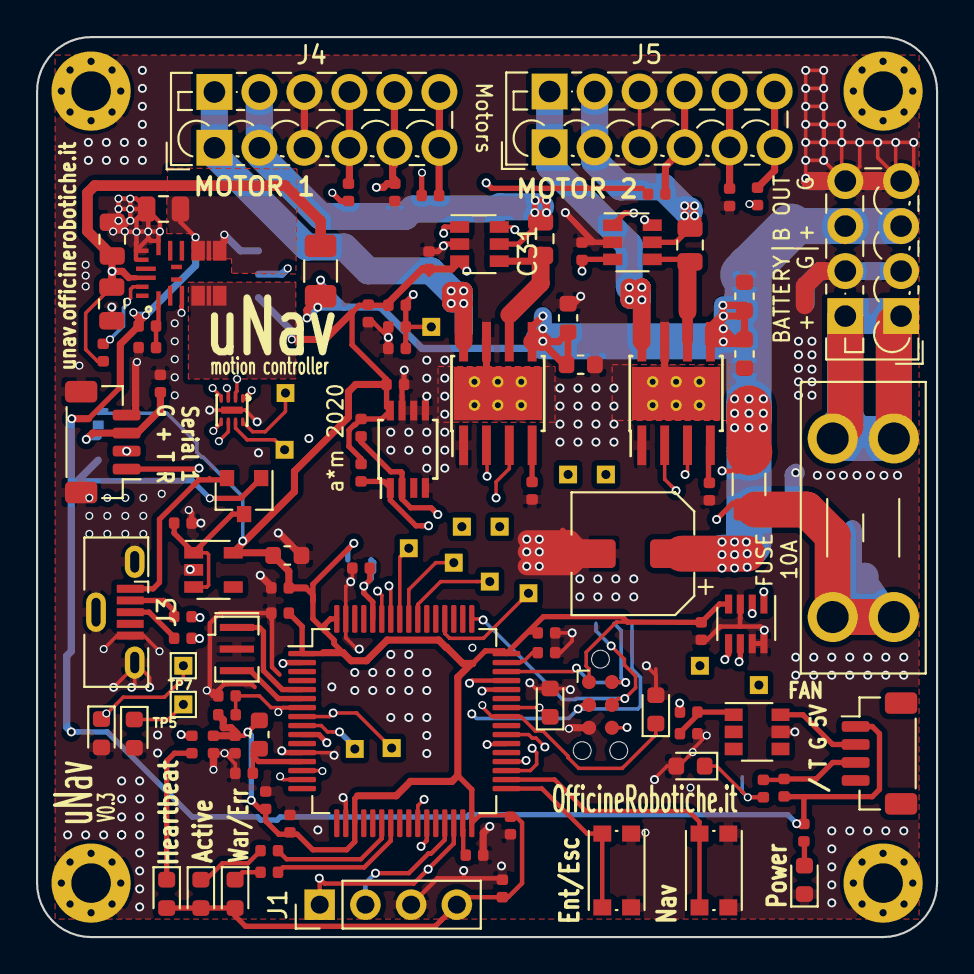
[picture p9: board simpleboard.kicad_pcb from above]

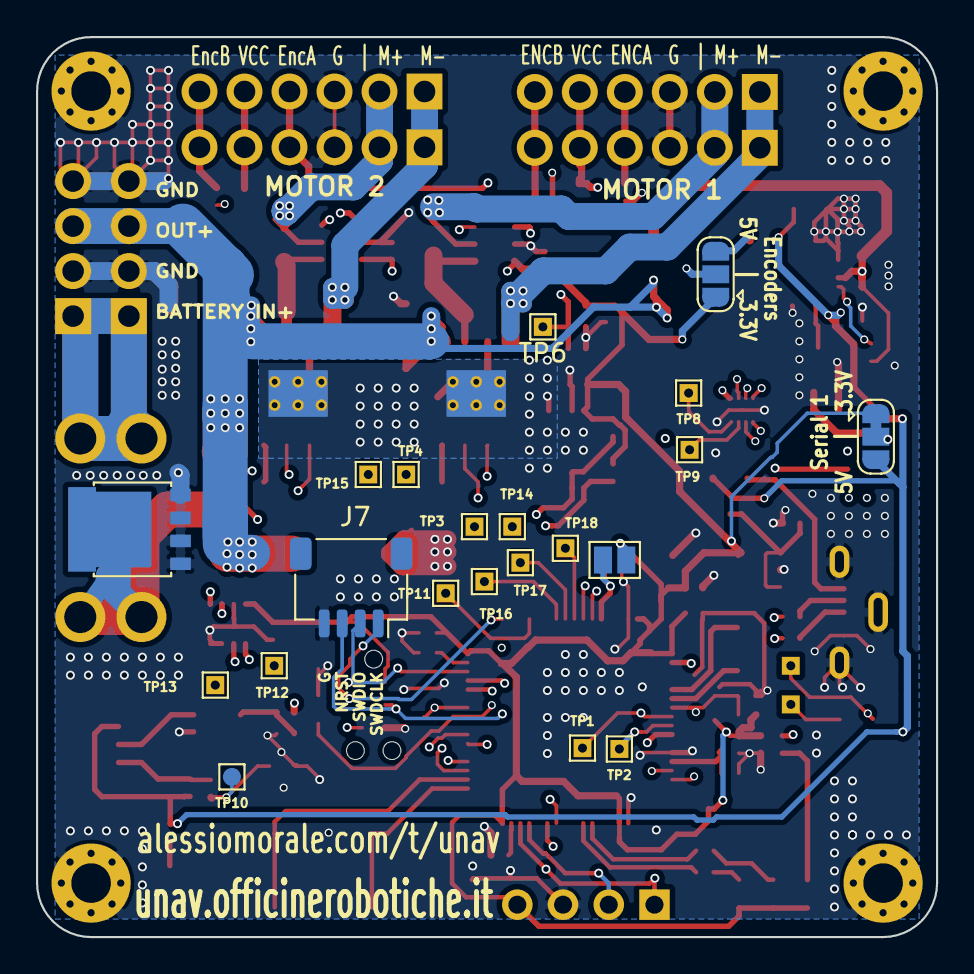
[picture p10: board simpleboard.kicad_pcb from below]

Board: 4 copper layers, 50.0 x 50.0 mm, 122 parts (21 on the bottom side), 76 nets.

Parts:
C1: 47uF; CP_Elec_6.3x5.8
C2, C5, C6, C7: 1uF 25V; C_0603_1608Metric
C3, C8, C9, C13, C14, C15, C16, C19, C21, C22, C23, C24, C26, C28, C29, C31, C32: 100nF 16V; C_0402_1005Metric
C4, C11, C12, C25, C27: 1uF 10V; C_0402_1005Metric
C10: 10n; C_0402_1005Metric
C17: 22uF 25V; C_0805_2012Metric
C18: 4.7uf 25V; C_0805_2012Metric
C20: 22uf 6.3V; C_0805_2012Metric
C30: 1uF 6.3V; C_0603_1608Metric
D1: Blue; LED_0603_1608Metric
D2: Yellow; LED_0603_1608Metric
D3: Red; LED_0603_1608Metric
D4: BAT54C; SOT-23
D5: green; LED_0603_1608Metric
D6: STPS3045DJF; LFPAK56
D7, D8, D9, D10: 3.3V; D_0603_1608Metric
D11: D_Zener; D_0603_1608Metric
F1: Fuse_Small; Fuseholder_Blade_Mini_Keystone_3568
F2: Polyfuse_Small; Fuse_1206_3216Metric
H1, H2, H3, H4: MountingHole; MountingHole_2.2mm_M2_Pad_Via
IC1: MPM36xx; QFN-20-MPS-3x5x1.6mm
IC2: IP4251; HUSON8
J1: OLED; PinHeader_1x04_P2.54mm_Vertical
J2: SERIAL1; JST_SH_BM04B-SRSS-TB_1x04-1MP_P1.00mm_Vertical
J3: USB_B_Micro; USB_Micro-B_Molex-105133-0001
J4: Motor1; TerminalBlock_Phoenix_PTSM-0,5-6-2.5-V-THR_1x06_P2.50mm_Ver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
J5: Motor2; TerminalBlock_Phoenix_PTSM-0,5-6-2.5-V-THR_1x06_P2.50mm_Ver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
J6: Battery; TerminalBlock_Phoenix_PTSM-0,5-4-2.5-V-THR_1x04_P2.50mm_Ver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
J7: SWD2; JST_SH_SM04B-SRSS-TB_1x04-1MP_P1.00mm_Horizontal
J8: FAN; JST_SH_BM04B-SRSS-TB_1x04-1MP_P1.00mm_Vertical
JP1: BOOT; SolderJumper-2_P1.3mm_Open_Pad1.0x1.5mm
JP2: S1_VSEL; SolderJumper-3_P1.3mm_Bridged12_RoundedPad1.0x1.5mm
JP3: Jumper_3_Bridged12; SolderJumper-3_P1.3mm_Open_RoundedPad1.0x1.5mm
L1: bead; L_0603_1608Metric
P1: SWD_TC; Tag-Connect_TC2030-IDC-NL_2x03_P1.27mm_Vertical
Q1: FDC6401N; SuperSOT-6
R1, R2, R11, R17, R18, R19, R20, R21, R28: 1k; R_0402_1005Metric
R3, R4: 15k; R_0402_1005Metric
R5, R6: 0.003; R_0805_2012Metric
R7, R8: 47k; R_0402_1005Metric
R9: 220; R_0402_1005Metric
R10: 10k; R_0402_1005Metric
R12: 0.001; R_1206_3216Metric
R13, R22, R23, R24: 330; R_0402_1005Metric
R14, R25: 4.7k; R_0402_1005Metric
R15: 100K; R_0402_1005Metric
R16: 19.1K; R_0402_1005Metric
R26, R27: 22; R_0402_1005Metric
SW1, SW2: KEY_UP; SW_Push_1P1T_NO_CK_KMR2
TP1, TP2, TP3, TP4, TP5, TP6, TP7, TP8, TP9, TP10, TP11, TP12, TP13, TP14, TP15, TP16, TP17, TP18: TestPoint; TestPoint_THTPad_1.0x1.0mm_Drill0.5mm
U1, U6: DRV8871DDA; Texas_HTSOP-8-1EP_3.9x4.9mm_P1.27mm_EP2.95x4.9mm_Mask2.4x3.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
U2: INA219AxDCN; SOT-23-8
U3: LM75B; TSSOP-8_3x3mm_P0.65mm
U4: AP2112K-3.3; SOT-23-5
U5: STM32F405RGTx; LQFP-64_10x10mm_P0.5mm
U7, U8: INA186; SOT-23-6
Y1: 8MHz; Resonator_SMD_muRata_CSTxExxV-3Pin_3.0x1.1mm

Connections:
+3V3: C8.2, C9.2, C13.2, C14.2, C15.1, C16.1, C21.2, C22.2, C23.2, C24.2, C25.2, C27.1, C28.2, C30.1, C32.2, D1.2, D2.2, D3.2, J1.4, JP1.1, JP2.1, JP3.1, L1.1, P1.1, R1.1, R7.1, R14.2, R25.2, U2.4, U3.8, U4.5, U5.1, U5.19, U5.32, U5.48, U5.64, U7.3, U8.3
+5V: C20.1, D4.1, IC1.7, IC1.8, IC1.9, J8.1, JP2.3, JP3.3, R10.2, R15.2, R17.2
/5V_USB: D4.2, J3.1
/ADC_MOT1_CUR: TP1.1, U5.8, U7.6
/ADC_MOT2_CUR: TP2.1, U5.9, U8.6
/ADC_VREF: C4.1, R1.2, R2.1, TP6.1, U5.10, U7.1, U8.1
/BATTERY+: F1.1, J6.1
/BOOT0: JP1.2, R8.1, U5.60
/I2C_SCL: J1.2, R25.1, TP12.1, U2.5, U3.2, U5.29
/I2C_SDA: J1.1, R14.1, TP13.1, U2.6, U3.1, U5.30
/I_KEY0: SW1.1, U5.33
/I_KEY1: SW2.1, U5.34
/NRST: C10.1, J7.3, P1.3, R7.2, U5.7
/O_LED1: R22.1, U5.2
/O_LED2: R23.1, U5.22
/O_LED3: R24.1, U5.23
/O_SPI_CS1: TP11.1, U5.52
/SER1_RX: J2.1, U5.59
/SER1_TX: J2.2, U5.58
/SPI1_MISO: TP17.1, U5.56
/SPI1_MOSI: TP18.1, U5.57
/SPI1_SCK: P1.6, TP16.1, U5.55
/SWCK: J7.1, P1.4, U5.49
/SWDIO: J7.2, P1.2, U5.46
/Sheet5E8E545F/ENC1_A: J4.4, R18.1
/Sheet5E8E545F/ENC1_B: J4.6, R20.1
/Sheet5E8E545F/ENC2_A: J5.4, R19.1
/Sheet5E8E545F/ENC2_B: J5.6, R21.1
/Sheet5E8E545F/ENC_Power: C3.2, C31.1, J4.5, J5.5, JP3.2
/Sheet5E94E0E4/MOT1_A: J4.2, R5.1, U7.5
/Sheet5E94E0E4/MOT1_B: J4.1, U1.8
/Sheet5E94E0E4/MOT2_A: J5.2, R6.1, U8.5
/Sheet5E94E0E4/MOT2_B: J5.1, U6.8
/Sheet5E8941DD/FAN_GND: J8.2, Q1.6
/Sheet5E8941DD/FAN_TACH: J8.3, R10.1, R28.1
/TIM_ENC1_A: D10.1, IC2.1, TP8.1, U5.41
/TIM_ENC1_B: D9.1, IC2.2, TP9.1, U5.42
/TIM_ENC2_A: D8.1, IC2.3, TP7.1, U5.14
/TIM_ENC2_B: D7.1, IC2.4, TP5.1, U5.15
/TIM_FAN_INDEX: D11.1, R28.2, TP10.1, U5.27
/TIM_FAN_PWM: R9.2, U5.26
/TIM_MOT1_A: TP3.1, U1.3, U5.38
/TIM_MOT1_B: TP14.1, U1.2, U5.35
/TIM_MOT2_A: TP4.1, U5.39, U6.3
/TIM_MOT2_B: TP15.1, U5.36, U6.2
/USB_OTG_FS_DM: R27.1, U5.44
/USB_OTG_FS_DP: R26.1, U5.45
/VDDA: C26.1, L1.2, U5.13
/V_BATT_INT: C17.1, C18.1, F2.1, IC1.16, R13.1
GND: C1.2, C2.2, C3.1, C4.2, C5.2, C6.2, C7.2, C8.1, C9.1, C10.2, C11.2, C12.2, C13.1, C14.1, C15.2, C16.2, C17.2, C18.2, C19.2, C20.2, C21.1, C22.1, C23.1, C24.1, C25.1, C26.2, C27.2, C28.1, C29.2, C30.2, C31.2, C32.1, D5.1, D6.1, D6.2, D6.3, D6.4, D7.2, D8.2, D9.2, D10.2, D11.2, H1.1, H2.1, H3.1, H4.1, IC1.3, IC1.12, IC1.13, IC1.14, IC2.9, J1.3, J2.4, J2.MP, J3.5, J3.6, J4.3, J5.3, J6.2, J6.4, J7.4, P1.5, Q1.5, R2.2, R3.2, R4.2, R8.2, R11.1, R16.1, SW1.2, SW2.2, U1.1, U1.7, U1.9, U2.3, U2.7, U2.8, U3.4, U3.5, U3.6, U3.7, U4.2, U5.12, U5.18, U5.63, U6.1, U6.7, U6.9, U7.2, U8.2, Y1.2
unnamed: C11.1, U5.31
unnamed: C12.1, U5.47
unnamed: C19.1, D4.3, U4.1, U4.3
unnamed: C29.1, J2.3, JP2.2
unnamed: D1.1, R22.2
unnamed: D2.1, R23.2
unnamed: D3.1, R24.2
unnamed: D5.2, R17.1
unnamed: D6.5, F1.2, R12.2, U2.1
unnamed: IC1.1, R15.1, R16.2
unnamed: IC1.4, IC1.5, IC1.6
unnamed: IC1.17, R13.2
unnamed: IC2.5, R21.2
unnamed: IC2.6, R19.2
unnamed: IC2.7, R20.2
unnamed: IC2.8, R18.2
unnamed: J3.2, R27.2
unnamed: J3.3, R26.2
unnamed: Q1.1, R9.1, R11.2
unnamed: R3.1, U1.4
unnamed: R4.1, U6.4
unnamed: R5.2, U1.6, U7.4
unnamed: R6.2, U6.6, U8.4
unnamed: U5.5, Y1.1
unnamed: U5.6, Y1.3
VBATT: C1.1, C2.1, C5.1, C6.1, C7.1, F2.2, J6.3, R12.1, U1.5, U2.2, U6.5

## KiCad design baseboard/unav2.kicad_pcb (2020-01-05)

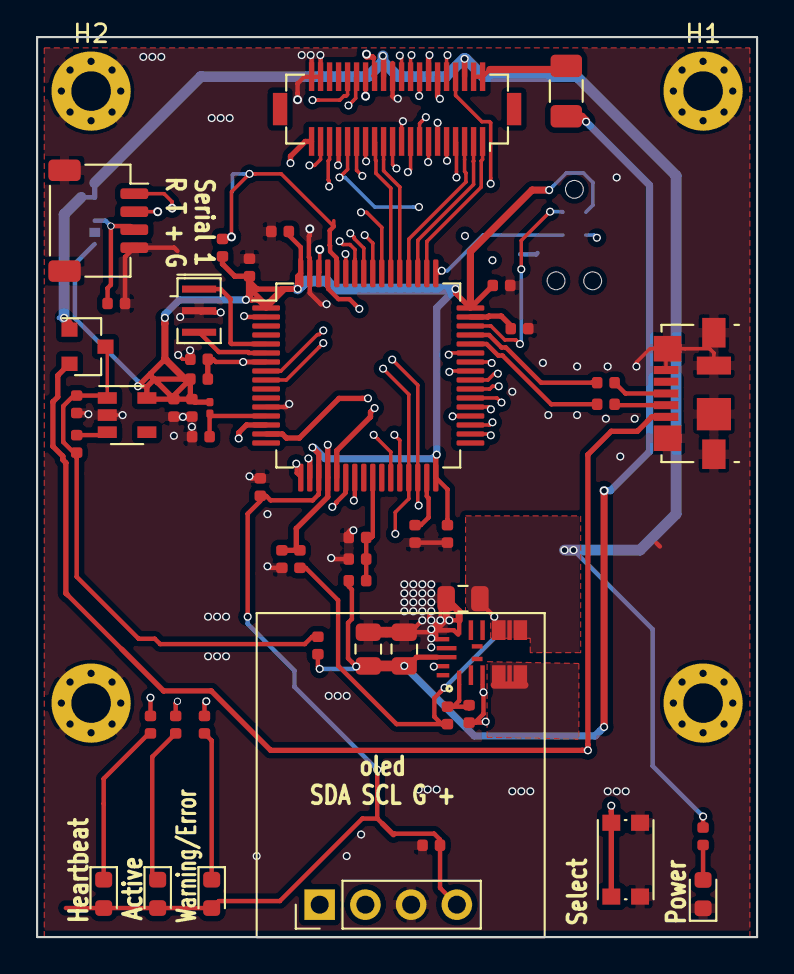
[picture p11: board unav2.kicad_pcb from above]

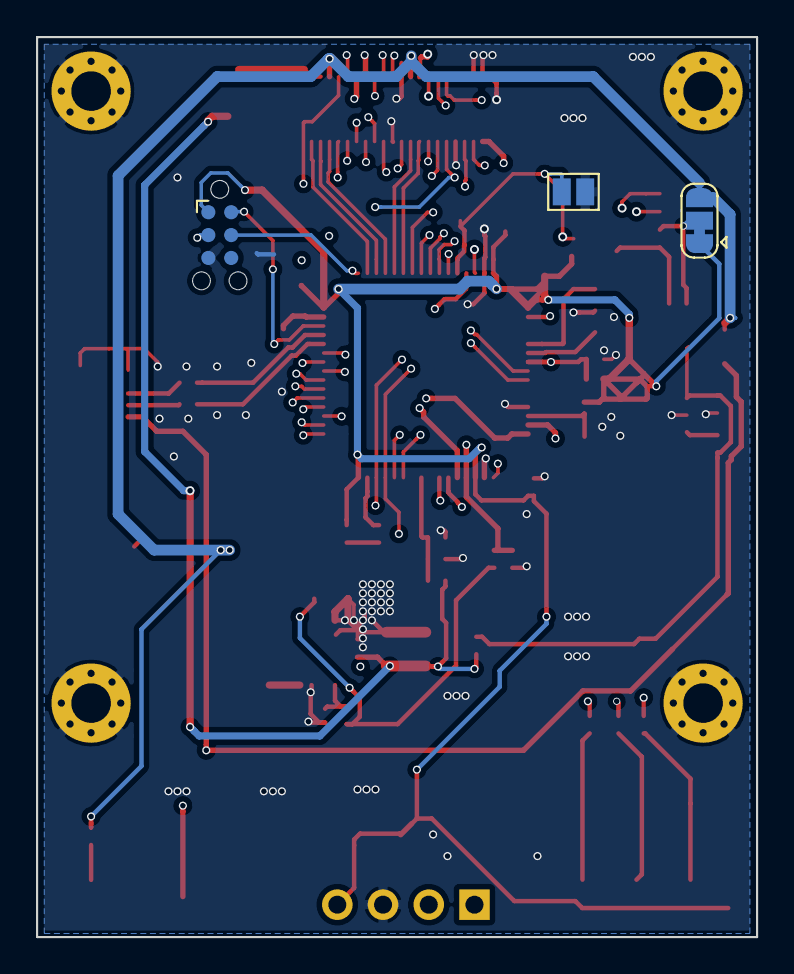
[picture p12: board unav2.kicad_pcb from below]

Board: 4 copper layers, 40.0 x 50.0 mm, 57 parts (3 on the bottom side), 65 nets.

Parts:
C3, C7, C13: 1uF; C_0402_1005Metric
C4, C5, C8, C9, C10, C11, C12, C14, C16, C18: 100nF; C_0402_1005Metric
C6, C22: C; C_0402_1005Metric
C15, C19: 4.7uf; C_0805_2012Metric
C17: 22uf; C_0805_2012Metric
C21: 10n; C_0402_1005Metric
D1: White; LED_0603_1608Metric
D2: BAT54C; SOT-23
D3: Blue; LED_0603_1608Metric
D4: Yellow; LED_0603_1608Metric
D5: Red; LED_0603_1608Metric
F1: Polyfuse_Small; Fuse_1206_3216Metric
H1, H2, H3, H4: MountingHole; MountingHole_2.2mm_M2_Pad_Via
IC1: MPM36xx; QFN-20-MPS-3x5x1.6mm
J1: Conn_02x20_Top_Bottom; Hirose_DF12_DF12B-40DS-0.5V(86)
J4: SERIAL1; JST_SH_SM04B-SRSS-TB_1x04-1MP_P1.00mm_Horizontal
J5: OLED; PinHeader_1x04_P2.54mm_Vertical
J6: USB_B_Micro; USB_Micro-B_Molex_47346-0001
JP1: BOOT; SolderJumper-2_P1.3mm_Open_Pad1.0x1.5mm
JP3: S1_VSEL; SolderJumper-3_P1.3mm_Bridged12_RoundedPad1.0x1.5mm
L1: L_Small; L_0201_0603Metric
P1: SWD_TC; Tag-Connect_TC2030-IDC-NL_2x03_P1.27mm_Vertical
R1: 49k; R_0402_1005Metric
R2, R17, R18, R19: 330; R_0402_1005Metric
R3: 10k; R_0402_1005Metric
R4, R5: 10K; R_0402_1005Metric
R6: 22K; R_0402_1005Metric
R7, R14: 47k; R_0402_1005Metric
R10: 22; R_0402_1005Metric
R15, R16: 1k; R_0402_1005Metric
SW1: KEY_UP; SW_Push_1P1T_NO_CK_KMR2
U1: STM32F405RGTx; LQFP-64_10x10mm_P0.5mm
U2: AP2121AK-3.3; SOT-23-5
Y1: 8MHz; Resonator_SMD_muRata_CSTxExxV-3Pin_3.0x1.1mm
e: 22; R_0402_1005Metric

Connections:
+3V3: C4.2, C6.2, C8.2, C9.2, C10.2, C11.2, C12.2, C13.2, D3.2, D4.2, D5.2, J5.4, JP3.1, L1.1, P1.1, R7.1, R14.1, U1.1, U1.19, U1.32, U1.48, U1.64, U2.5
+5V: C17.1, D2.1, IC1.7, IC1.8, IC1.9, J1.23, J1.32, JP3.3, R4.2, R6.2, R16.2
/5V_USB: D2.2, J6.1
/ADC_BATT_VOL: C5.1, R1.1, R15.2, U1.25
/ADC_MOT1_CUR: J1.18, U1.8
/ADC_MOT2_CUR: J1.19, U1.9
/BOOT0: JP1.2, R7.2, U1.60
/I2C_SCL: J1.15, J5.2, U1.29
/I2C_SDA: J1.14, J5.1, U1.30
/I_FAN_INDEX: J1.29, U1.28
/I_FAULT: C18.1, J1.20, R6.1, U1.20
/I_KEY_UP: SW1.1, U1.14
/I_MOT_FAULT: J1.11, U1.34
/NRST: C21.1, P1.3, R14.2, U1.7
/O_LED1: R17.1, U1.2
/O_LED2: R18.1, U1.22
/O_LED3: R19.1, U1.23
/O_MOT_ENABLE: J1.7, U1.37
/O_PWR_MOT_EN: J1.16, U1.43
/O_PWR_SBC_EN: J1.4, U1.40
/O_REG_EN: IC1.17, U1.61
/O_SPI_CS1: J1.3, U1.52
/O_SPI_CS2: J1.2, U1.51
/PA15: J1.1, U1.50
/SER1_RX: J4.1, U1.59
/SER1_TX: J4.2, U1.58
/SER2_RX: J1.13, U1.54
/SER2_TX: J1.12, U1.53
/SPARE_1: J1.33, U1.17
/SPI1_MISO: J1.35, U1.56
/SPI1_MOSI: J1.36, U1.57
/SPI1_SCK: J1.34, U1.55
/SWCK: P1.4, U1.49
/SWDIO: P1.2, U1.46
/TIM_AUX2_PWM: J1.28, U1.62
/TIM_ENC1_A: J1.24, U1.41
/TIM_ENC1_B: J1.25, U1.42
/TIM_ENC2_A: J1.26, U1.21
/TIM_ENC2_B: J1.27, U1.15
/TIM_FAN_PWM: J1.30, U1.27
/TIM_MOT1_A: J1.6, U1.38
/TIM_MOT1_B: J1.9, U1.35
/TIM_MOT2_A: J1.5, U1.39
/TIM_MOT2_B: J1.8, U1.36
/USB_OTG_FS_DM: R10.1, U1.44
/USB_OTG_FS_DP: U1.45, e.1
/V_BATT: C15.1, C19.1, F1.1, IC1.16, R1.2, R2.2
GND: C3.2, C4.1, C5.2, C6.1, C7.2, C8.1, C9.1, C10.1, C11.1, C12.1, C13.1, C14.2, C15.2, C16.2, C17.2, C18.2, C19.2, C21.2, C22.2, D1.1, H1.1, H2.1, H3.1, H4.1, IC1.3, IC1.12, IC1.13, IC1.14, J1.10, J1.17, J1.31, J1.39, J1.40, J4.4, J4.MP, J5.3, J6.5, J6.6, JP1.1, P1.5, R5.1, R15.1, SW1.2, U1.12, U1.18, U1.63, U2.2, Y1.2
unnamed: C3.1, U1.31
unnamed: C7.1, U1.47
unnamed: C14.1, L1.2, U1.13
unnamed: C16.1, D2.3, R2.1, R3.1, U2.1
unnamed: C22.1, J4.3, JP3.2
unnamed: D1.2, R16.1
unnamed: D3.1, R17.2
unnamed: D4.1, R18.2
unnamed: D5.1, R19.2
unnamed: F1.2, J1.21, J1.22
unnamed: IC1.1, R4.1, R5.2
unnamed: IC1.4, IC1.5, IC1.6
unnamed: J6.2, R10.2
unnamed: J6.3, e.2
unnamed: R3.2, U2.3
unnamed: U1.5, Y1.1
unnamed: U1.6, Y1.3

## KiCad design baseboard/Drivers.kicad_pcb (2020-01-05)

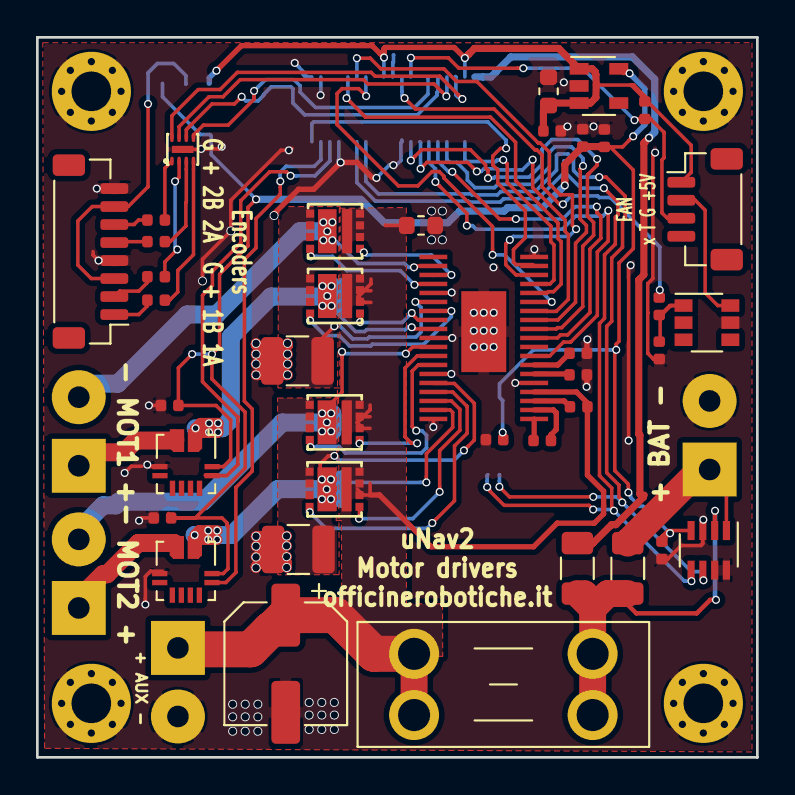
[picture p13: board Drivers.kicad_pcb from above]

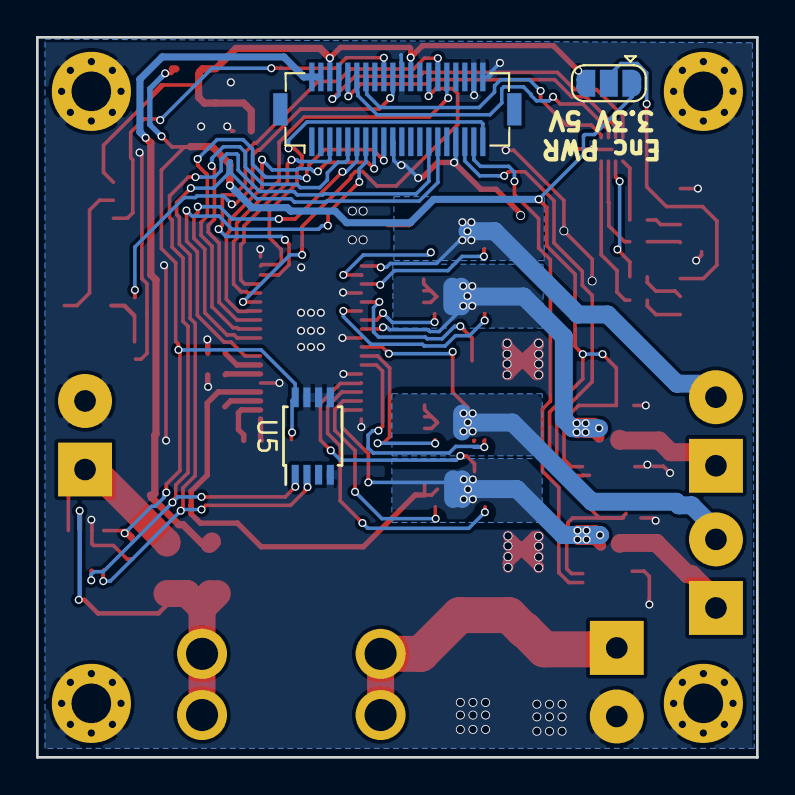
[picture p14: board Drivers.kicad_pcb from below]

Board: 2 copper layers, 40.0 x 40.0 mm, 50 parts (3 on the bottom side), 59 nets.

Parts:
C1, C7: 1uF; C_0603_1608Metric
C2, C3, C4, C14: 100n; C_0402_1005Metric
C5: 1uF; C_0402_1005Metric
C6: 47uF; CP_Elec_6.3x5.8
C8, C9: 100nF; C_0402_1005Metric
C10, C11: 0.1uF 20V X7R; C_0402_1005Metric
C12, C13: 1uF 16V X7R; C_0402_1005Metric
F1: Fuse_Small; Fuseholder_Blade_Mini_Keystone_3568
F2: Polyfuse_Small; Fuse_1206_3216Metric
H1, H2, H3, H4: MountingHole; MountingHole_2.2mm_M2_Pad_Via
IC1: IP4251; HUSON8
IC2: DRV8704; HTSSOP-38
J1: Conn_02x20_Top_Bottom; Hirose_DF12_DF12B(3.5)-40DP-0.5V(86)
J2: M1; SolderWirePad_1x02_P3.81mm_Drill1.2mm
J3: M2; SolderWirePad_1x02_P3.81mm_Drill1.2mm
J4: Battery; SolderWirePad_1x02_P3.81mm_Drill1.2mm
J5: SBC; SolderWirePad_1x02_P3.81mm_Drill1.2mm
J6: Enc; JST_SH_BM08B-SRSS-TB_1x08-1MP_P1.00mm_Vertical
J7: FAN; JST_SH_BM04B-SRSS-TB_1x04-1MP_P1.00mm_Vertical
JP1: Jumper_3_Bridged12; SolderJumper-3_P1.3mm_Open_RoundedPad1.0x1.5mm
Q1, Q2, Q3, Q4: SiZ340DT; PowerPair-3x3
Q5: Q_DUAL_NMOS_G1S2G2D2S1D1; SuperSOT-6
R1: 0.01; R_1206_3216Metric
R2, R3, R4, R5: 1K; R_0402_1005Metric
R6, R7: R_Small; R_1210_3225Metric
R8: 220; R_0402_1005Metric
R9: 10k; R_0402_1005Metric
R10: 1k; R_0402_1005Metric
U1: INA219AxDCN; SOT-23-8
U2: AP2112K-3.3; SOT-23-5
U3, U4: ACS711xEXLT-31AB; Allegro_QFN-12-10-1EP_3x3mm_P0.5mm
U5: LM75B; TSSOP-8_3x3mm_P0.65mm

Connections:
+3V3: C3.1, C4.1, C5.1, C8.1, C9.1, C14.1, JP1.1, U1.4, U2.5, U3.10, U4.10, U5.8
+5V: C1.1, C2.1, J1.23, J1.32, J7.1, JP1.3, R9.2, U2.1, U2.3
/ADC_MOT1_CUR: J1.18, U3.9
/ADC_MOT2_CUR: J1.19, U4.9
/BATTERY+: J4.1, R1.2, U1.1
/I2C_SCL: J1.15, U1.5, U5.2
/I2C_SDA: J1.14, U1.6, U5.1
/I_FAN_INDEX: J1.29, J7.3, R9.1
/I_FAULT: IC2.18, J1.20
/O_MOT_ENABLE: IC2.8, J1.7
/O_SPI_CS1: IC2.16, J1.3
/SPI1_MISO: IC2.17, J1.35
/SPI1_MOSI: IC2.15, J1.36
/SPI1_SCK: IC2.14, J1.34
/Sheet5E8E545F/ENC1_A: J6.1, R2.1
/Sheet5E8E545F/ENC1_B: J6.2, R4.1
/Sheet5E8E545F/ENC2_A: J6.5, R3.1
/Sheet5E8E545F/ENC2_B: J6.6, R5.1
/Sheet5E8E545F/ENC_Power: J6.3, J6.7, JP1.2
/Sheet5E94E0E4/MOT1_A: J2.1, U3.2
/Sheet5E94E0E4/MOT1_B: IC2.21, J2.2, Q3.S1D2
/Sheet5E94E0E4/MOT2_A: J3.1, U4.2
/Sheet5E94E0E4/MOT2_B: IC2.30, J3.2, Q4.S1D2
/Sheet5E8941DD/FAN_GND: J7.2, Q5.6
/TIM_ENC1_A: IC1.1, J1.24
/TIM_ENC1_B: IC1.2, J1.25
/TIM_ENC2_A: IC1.3, J1.26
/TIM_ENC2_B: IC1.4, J1.27
/TIM_FAN_PWM: J1.30, R8.2
/TIM_MOT1_A: IC2.10, J1.6
/TIM_MOT1_B: IC2.11, J1.9
/TIM_MOT2_A: IC2.12, J1.5
/TIM_MOT2_B: IC2.13, J1.8
/V_BATT: C6.1, C7.1, C12.2, F1.2, IC2.4, J5.1, Q1.D1, Q2.D1, Q3.D1, Q4.D1
/V_BATT_INT: F2.1, J1.21, J1.22
GND: C1.2, C2.2, C3.2, C4.2, C5.2, C6.2, C7.2, C8.2, C9.2, C10.2, C13.2, C14.2, H1.1, H2.1, H3.1, H4.1, IC1.9, IC2.5, IC2.19, IC2.24, IC2.29, IC2.33, IC2.38, IC2.39, J1.10, J1.17, J1.31, J1.39, J1.40, J4.2, J5.2, J6.4, J6.8, Q5.5, R6.2, R7.2, R10.1, U1.3, U1.7, U1.8, U2.2, U3.3, U4.3, U5.4, U5.5, U5.6, U5.7
unnamed: C10.1, IC2.7
unnamed: C11.1, IC2.1
unnamed: C11.2, IC2.2
unnamed: C12.1, IC2.3
unnamed: C13.1, IC2.6
unnamed: F1.1, F2.2, R1.1, U1.2
unnamed: IC1.5, R2.2
unnamed: IC1.6, R3.2
unnamed: IC1.7, R4.2
unnamed: IC1.8, R5.2
unnamed: IC2.22, Q3.G1
unnamed: IC2.23, Q3.G2
unnamed: IC2.25, Q1.S2, Q3.S2, R6.1
unnamed: IC2.26, Q1.G2
unnamed: IC2.27, Q1.G1
unnamed: IC2.28, Q1.S1D2, U3.1
unnamed: IC2.31, Q4.G1
unnamed: IC2.32, Q4.G2
unnamed: IC2.34, Q2.S2, Q4.S2, R7.1
unnamed: IC2.35, Q2.G2
unnamed: IC2.36, Q2.G1
unnamed: IC2.37, Q2.S1D2, U4.1
unnamed: Q5.1, R8.1, R10.2

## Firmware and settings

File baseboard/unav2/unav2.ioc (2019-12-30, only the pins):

Mcu.UserName=STM32F407VETx
PA0-WKUP.GPIO_Label=I_KEY_UP
PA0-WKUP.Signal=GPXTI0
PA1.GPIO_Label=TIM_ENC2_A
PA1.Signal=S_TIM2_CH2
PA11.Signal=USB_OTG_FS_DM
PA12.Signal=USB_OTG_FS_DP
PA13.Signal=SYS_JTMS-SWDIO
PA14.Signal=SYS_JTCK-SWCLK
PA2.GPIO_Label=ADC_TEMP
PA2.Signal=ADCx_IN2
PA3.Signal=ADCx_IN3
PA5.GPIO_Label=TIM_ENC2_B
PA5.Signal=S_TIM2_CH1_ETR
PA6.GPIO_Label=O_LED1
PA6.Signal=S_TIM13_CH1
PA7.GPIO_Label=O_LED2
PA7.Signal=S_TIM14_CH1
PA8.Signal=S_TIM1_CH1
PA9.GPIO_Label=TIM_MOT2_A
PA9.Signal=S_TIM1_CH2
PB0.GPIO_Label=O_FLASH_CS
PB0.Signal=GPIO_Output
PB1.GPIO_Label=O_SPI_CS2
PB1.Signal=GPIO_Output
PB10.Signal=USART3_TX
PB11.Signal=USART3_RX
PB12.GPIO_Label=I_MOT_FAULT1
PB12.Signal=GPXTI12
PB14.GPIO_Label=TIM_MOT2_B
PB14.Signal=TIM1_CH2N
PB15.GPIO_Label=TIM_MOT1_B
PB15.Signal=TIM1_CH3N
PB3.Signal=SPI1_SCK
PB4.Signal=SPI1_MISO
PB5.Signal=SPI1_MOSI
PB6.Signal=I2C1_SCL
PB7.Signal=I2C1_SDA
PB8.GPIO_Label=O_PWR_EN
PB8.Signal=GPIO_Output
PB9.GPIO_Label=TIM_AUX_PWM
PB9.Signal=S_TIM11_CH1
PC0.GPIO_Label=ADC_MOT1_CUR
PC0.Signal=ADCx_IN10
PC1.GPIO_Label=ADC_MOT2_CUR
PC1.Signal=ADCx_IN11
PC13-ANTI_TAMP.GPIO_Label=I_FAN_INDEX
PC13-ANTI_TAMP.Signal=GPIO_Input
PC14-OSC32_IN.Signal=RCC_OSC32_IN
PC15-OSC32_OUT.Signal=RCC_OSC32_OUT
PC3.Signal=ADCx_IN13
PC4.GPIO_Label=ADC_BATT_CUR
PC4.Signal=ADCx_IN14
PC5.GPIO_Label=ADC_BATT_VOL
PC5.Signal=ADCx_IN15
PC6.GPIO_Label=TIM_ENC1_A
PC6.Signal=S_TIM3_CH1
PC7.GPIO_Label=TIM_MOT1_A
PC7.Signal=S_TIM8_CH2
PC8.GPIO_Label=TIM_MOT2_A
PC8.Signal=S_TIM8_CH3
PD10.GPIO_Label=IO_AUX2
PD10.Signal=GPIO_Input
PD11.GPIO_Label=IO_AUX1
PD11.Signal=GPIO_Output
PD5.Signal=USART2_TX
PD6.Signal=USART2_RX
PE0.GPIO_Label=O_PWR_MOT_EN
PE0.Signal=GPIO_Output
PE1.GPIO_Label=O_PWR_SBC_EN
PE1.Signal=GPIO_Output
PE13.Signal=S_TIM1_CH3
PE14.GPIO_Label=O_MOT_ENABLE
PE14.Signal=GPIO_Output
PE3.GPIO_Label=I_KEY1
PE3.Signal=GPIO_Input
PE4.GPIO_Label=I_KEY0
PE4.Signal=GPIO_Input
PE5.GPIO_Label=TIM_FAN_PWM
PE5.Signal=S_TIM9_CH1
PE6.GPIO_Label=TIM_AUX3_PWM
PE6.Signal=S_TIM9_CH2
PE7.GPIO_Label=O_SPI_CS3
PE7.Signal=GPIO_Output
PH0-OSC_IN.Signal=RCC_OSC_IN
PH1-OSC_OUT.Signal=RCC_OSC_OUT

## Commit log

2018-06-05 Initial commit for carrier prototype
    [carrier.kicad_pcb, carrier.sch]
2018-07-12 updated schematic
    [Drivers.sch, Encoders.sch, Power.sch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]
2018-07-15 update schematic
    [Drivers.sch, Encoders.sch, Power.sch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]
2018-07-16 Fix supply, add gps/imu serial, oled
    [Drivers.sch, Power.sch, carrier.sch]
2018-07-19 Schematic update
    [Drivers.sch, Power.sch, carrier.sch]
2018-07-24 Driver drv8704
    [Driver.sch, drv8704.kicad_pcb, drv8704.sch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]
2018-07-26 driver/supply board
    [Driver.sch, Power.sch, drv8704.kicad_pcb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]
2018-12-17 [UNAV2] - initial design, standalone
    [Drivers.sch, Encoders.sch, Power.sch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]
2018-12-17 [UNAV2] - initial draft of drv8704 based driver
    [drv8704.kicad_pcb]
2019-01-04 standalone version of unav2 based on stm32f405rgt
    [Drivers.sch, Power.sch, unav2.sch]
2019-12-30 rev 0
    [encoders.sch, input_outputs.sch, motor_control.sch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]
2020-01-05 Cleanup old designs
    [Driver.sch, Drivers.sch, Encoders.sch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]
2020-01-05 test design of mcu+driver boards(do not build!! it is just less than an idea right now)
    [Drivers.kicad_pcb, driver_encoder.sch, driver_encoders.sch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]
2020-01-05 Add integrated board design, to be used as an initial prototype to develop the fw
    [Encoders.sch, Power.sch, driver_encoder.sch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]
2020-01-05 add script to export to pdf, include pdf schematic
2020-01-05 Add supply inversion protection diode, move custom symbol to project lib
    [simpleboard.kicad_pcb, supply_term.sch]
2020-01-07 Beta 1 (move fan tach pin to a timer input)
    [encoders.sch, motordrivers.sch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]
2020-01-07 update pdf schematic
2020-01-25 Fix BOM
    [motordrivers.sch, simpleboard.sch, supply_term.sch]
2020-01-25 Add interactive BOM export (via the awesome https://github.com/openscopeproject/InteractiveHtmlBom plugin)
2020-01-25 Link bom (via htmlpreview) to the README.md
2020-02-04 Fixes for #1, #3, #4 & #6
    [encoders.sch, simpleboard.kicad_pcb, simpleboard.sch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]
2020-06-04 Additional fixes
    [simpleboard.kicad_pcb, supply_term.sch]
2020-08-10 V 0.3: - use a 6 pins connector for each motor - use vertical connectors for usb and serial - additional jst/sh for swt in the back of the board - additional stitching on ground plane
    [simpleboard.kicad_pcb, simpleboard.sch]
2020-08-10 V 0.3: update pdf, gerbers and rendering
    [simpleboard-B_Cu.gbr, simpleboard-B_Mask.gbr, simpleboard-B_Paste.gbr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]
